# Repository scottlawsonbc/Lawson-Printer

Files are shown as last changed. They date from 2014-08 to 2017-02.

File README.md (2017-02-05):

# Lawson-Printer
Open source high precision 3D printer

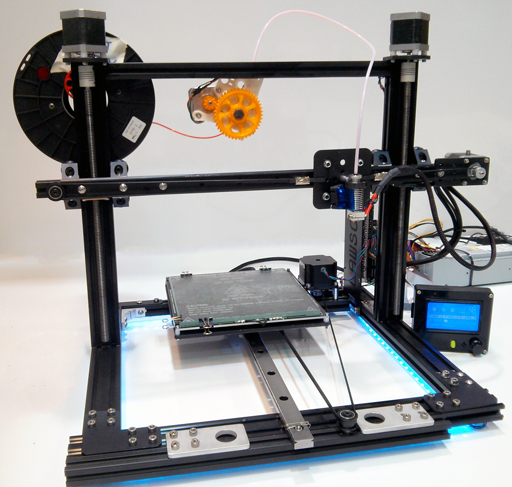
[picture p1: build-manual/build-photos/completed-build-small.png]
completed build


# Introduction
Lawson is a 3D printer design by [Scott Lawson](https://github.com/scottlawsonbc) featuring excellent linear motion accuracy and a mechanically stiff frame. Compared with the MendelMax 2, Lawson eliminates the need for custom sheet metal, slashes build costs, and improves the linear motion of the X, Y, and Z axes. It is easy to source components for the Lawson printer as 95% of the components can be sourced from only two suppliers.

# Overview

## Design Goals
* High accuracy linear motion
* Mechanically stiff frame
* All printable components have purchasable off-the-shelf counterparts
* Easy to source components. 95% of components available from two suppliers to simplify component sourcing

## Cost
The total build cost of the Lawson printer is approximately $900 USD. This is the price for all components needed to build a working Lawson printer including electronics and [[Stepper motor|motors]]. Build costs can be reduced by approximately $120 USD if printed components are used.

## Component Sourcing
See [Lawson Buyer's Guide](http://reprap.org/wiki/Lawson_Buyers_Guide) for component sourcing information.

To simplify component sourcing, 95% of the components can be obtained from only just two suppliers, Misumi and OpenBuilds Parts Store. The parts that cannot be obtained from these suppliers are:
* Hotend + Extruder
* Heated bed + Glass
* Electronics

This gives users the freedom to easily purchase Lawson components themselves, without needing to go through a middle-man supplier selling a kit. 

## X-axis
The x-axis is a belt driven linear stage powered by a NEMA 17 Stepper motor. The axis is constrained by OpenRail which is screwed into a length of 2020 aluminium extrusion. The x-carriage wheels have eccentric spacers that can be adjusted to prevent excessive friction. The belt tension can be adjusted easily by loosening the belt idler and sliding it left or right on the extrusion. While a direct drive extruder can be used, a bowden feed extruder is reccommended because it significantly reduces the mass of the x-carriage, permitting higher acceleration and speed values and reducing resonance.

## Y-axis

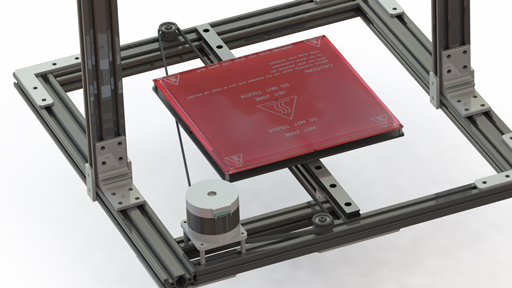
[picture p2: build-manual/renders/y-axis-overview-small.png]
y-axis mechanism


The y-axis is a belt driven linear stage powered by a NEMA 23 Stepper motor and is constrained by a precision Misumi linear slide. Compared to y-axes in other designs such as the MendelMax 2, this triangular belt configuration permits higher speed and acceleration values, reduces component costs, and simplifies construction and maintenance access. The y-axis belt tension can be adjusted by loosening the screws on the NEMA 23 motor and sliding the motor left or right.

The NEMA 23 was selected instead of a NEMA 17 because it permits a simplified mounting configuration and has generally higher performance characteristics.

## Z-axis
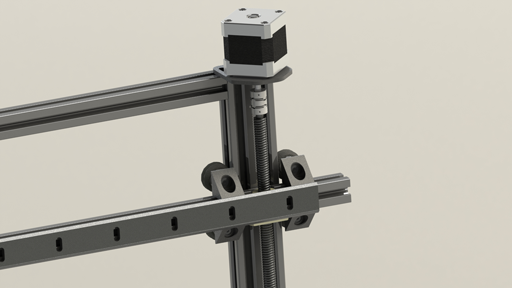
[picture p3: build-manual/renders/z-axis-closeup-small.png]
z-axis closeup


The z-axis is a lead screw driven linear stage powered by two NEMA 17 Stepper motor wired in parallel. The z-axis is accurate to ±150 µm over the full travel. The wheels have eccentric spacers that can be adjusted to prevent excessive friction from overconstaint. 

### Comparison to MendelMax 2
The lead screws in the Lawson printer design have the following accuracy specification:
* ±20µm per revolution (due to [thread drunkeness](http://www.deterco.com/tech_info/conversion/helical.htm))
* ±150µm/300mm accumulated pitch error

In comparison, there is no accuracy specification available for the lead screws that the MendelMax 2 design calls for. As such, the accuracy of the MendelMax 2 lead z-axis cannot be guaranteed.

> Unfortunately our lead screws do not have a tolerance specification for these dimensions. These are medium-grade leadscrews, they are better than the cheap screwes[sic] many people use on 3d printers, but they are not comparable to more expensive high end leadscrews. -Mike [from MakersToolWorks]

## Printable Components
Printable components are highlighted in blue

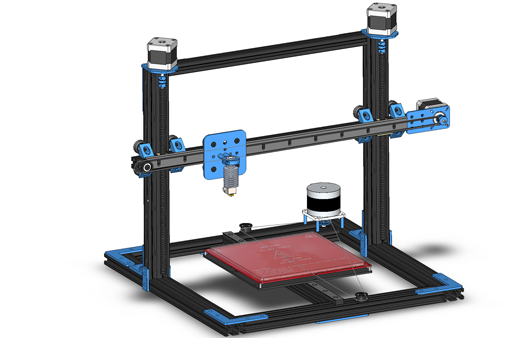
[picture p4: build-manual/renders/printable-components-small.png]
printable components


A number of Lawson components can be 3D printed to reduce build costs, with the caveat that printed components are less stiff than their metal counterparts. Unlike many other RepRap printers, *all printable components are purchasable, but not all purchasable components are printable*. This means that printed components are not mandatory and that individuals without access to 3D printers, or individuals who prefer metal components are able to build a Lawson printer. The use of printed components can save up to approximately $120 USD in build costs.

Printable components:
* **Qty:** 2 **Part:** Heavy duty bracket
* **Qty:** 1 **Part:** GT2 Pulley GPA22GT2060-B-H4
* **Qty:** 1 **Part:** Shaft collar
* **Qty:** 4 **Part:** 2-hole Thin bracket HBLSS5
* **Qty:** 2 **Part:** 4-hole bracket HPTSSL5
* **Qty:** 2 **Part:** 8-hole L bracket HPTLD5
* **Qty:** 4 **Part:** 4-hole L bracket HPTLS5
* **Qty:** 2 **Part:** 4-hole T bracket HPTTS5
* **Qty:** 6 **Part:** 2-hole joining plate
* **Qty:** 1 **Part:** 20mm gantry plate
* **Qty:** 8 **Part:** 90deg vslot corner connector
* **Qty:** 2 **Part:** 5mm x 6mm coupler
* **Qty:** 4 **Part:** Belt crimp clamp

## Electronics
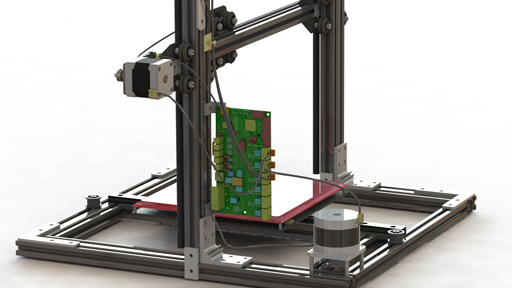
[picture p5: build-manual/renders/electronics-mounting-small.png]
electronics mounting


Almost all RepRap electronics such can be used to control the Lawson. Electronics confirmed to be working include RUMBA, Printrboard, Generation 7 Electronics, Arduino Mega Pololu Shield, and Rambo.

One option for mounting electronics is the rear side of the z-axis aluminium extrusion. The electronics can be conveniently mounted close to the motors and endstops if mounting is on the same side as the x-axis and y-axis motors. With this configuration, there is easy access to the electronics for wiring any maintenance that may be required.

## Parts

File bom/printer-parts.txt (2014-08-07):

REQUIRED PARTS:

	Heavy duty brackets: 		HBLTDW5
	Aluminium extrusion:			HFS5-2060-300
	Linear slide:						SEL2BM20-400
	Spacers:							SMKB4-20

	Belt idler:							http://openbuildspartstore.com/smooth-idler-pulley-kit/
	Belt clamp:						http://openbuildspartstore.com/belt-crimp-clamp/

OPTIONAL PARTS:
	Heat insulating sheets 200x400mm: 				HIFP1-400-200

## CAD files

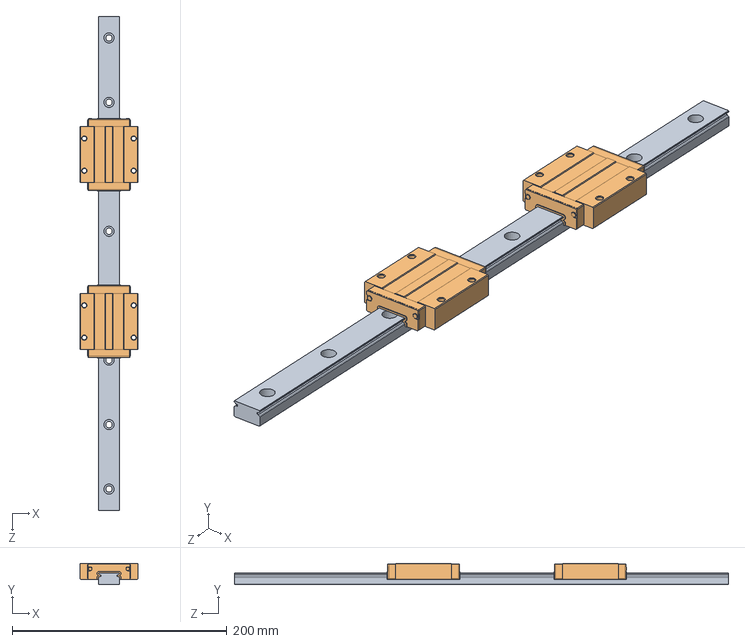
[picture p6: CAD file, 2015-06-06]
solidworks/y-axis-assembly/slide/SEL2BM20-460.sldasm
54.0 x 20.0 x 460.0 mm
SE2BM20-460_r
ELBM20_b x 2

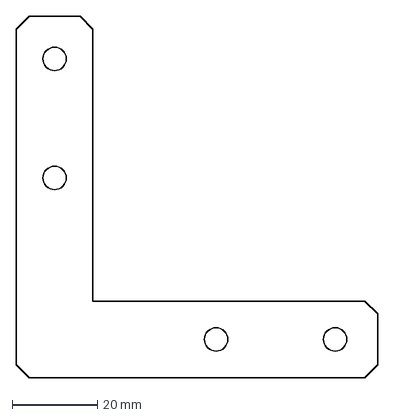
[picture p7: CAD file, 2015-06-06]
dxf-files/4 Hole L Bracket.DXF
85.0 x 85.0 mm

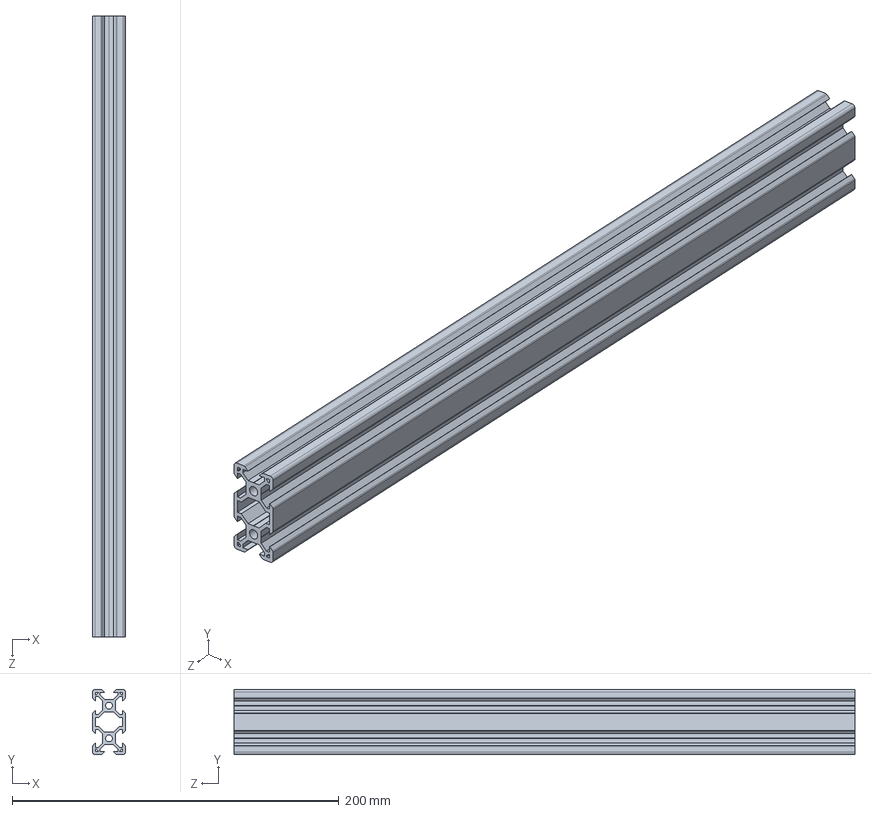
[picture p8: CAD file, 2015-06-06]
solidworks/aluminium-extrusion/openbuilds-extrusion/vslot-2040.SLDPRT
20.0 x 40.0 x 380.0 mm

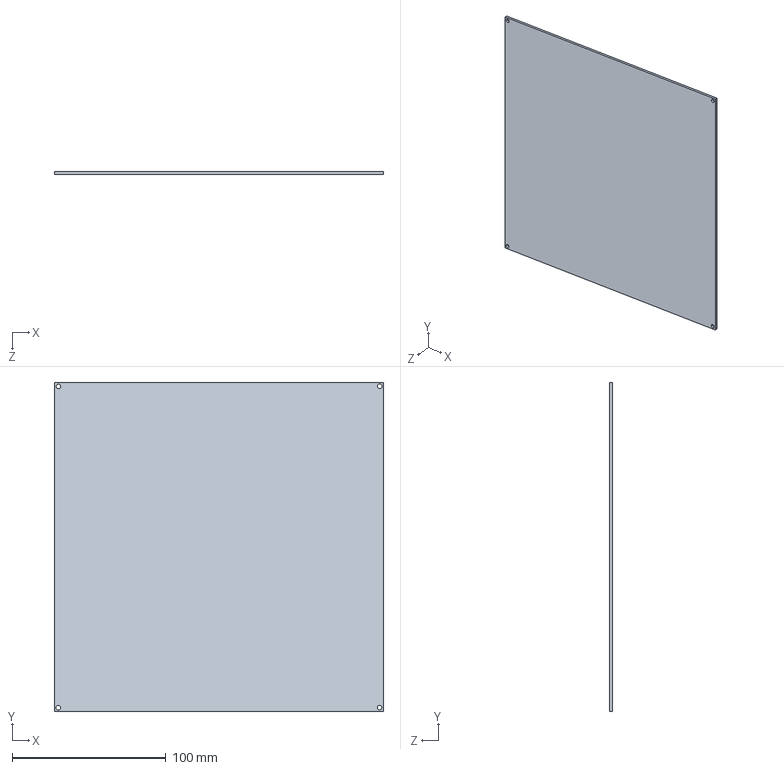
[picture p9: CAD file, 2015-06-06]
solidworks/y-axis-assembly/print-bed/heated-bed.SLDPRT
214.0 x 214.0 x 2.00 mm

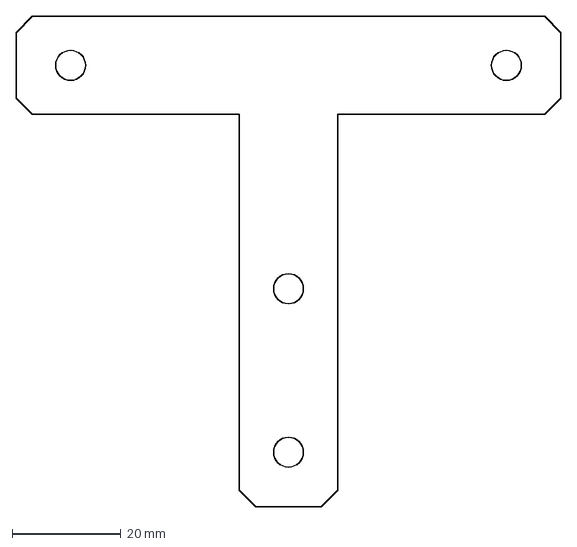
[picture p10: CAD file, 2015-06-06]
dxf-files/4 Hole T Bracket.DXF
100.0 x 90.0 mm

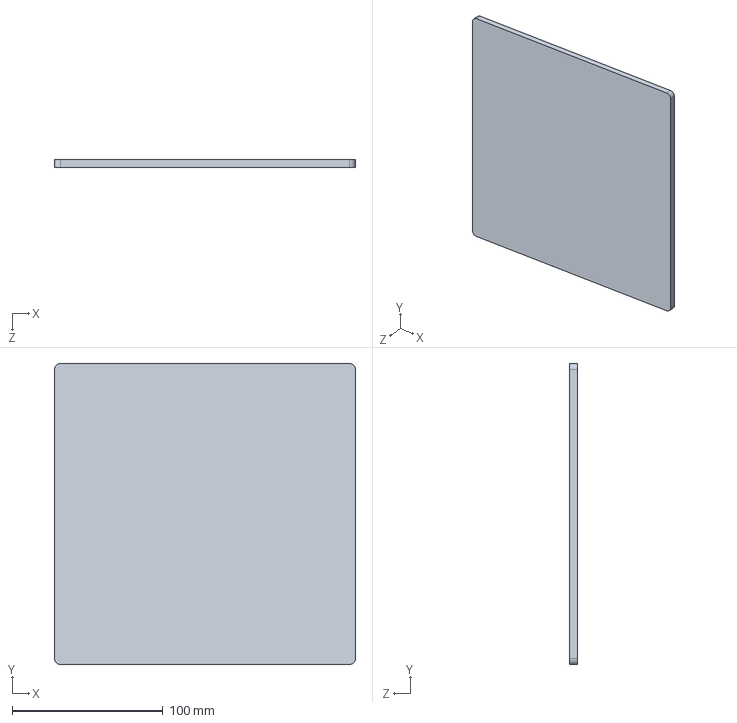
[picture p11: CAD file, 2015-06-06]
solidworks/y-axis-assembly/print-bed/glass-bed.SLDPRT
200.0 x 200.0 x 5.00 mm

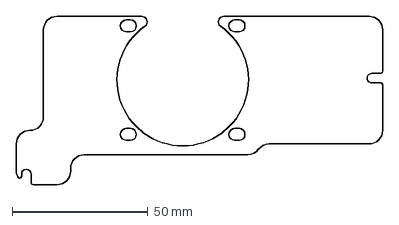
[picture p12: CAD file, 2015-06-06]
dxf-files/electronics-fan-mount.DXF
135.0 x 62.0 mm

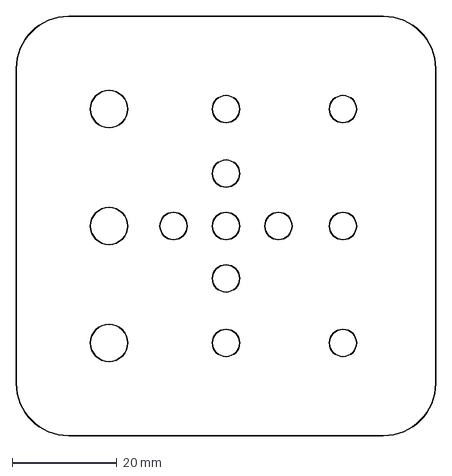
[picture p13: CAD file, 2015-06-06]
dxf-files/OpenRail Universal Gantry Plate - 20mm.DXF
80.0 x 80.0 mm

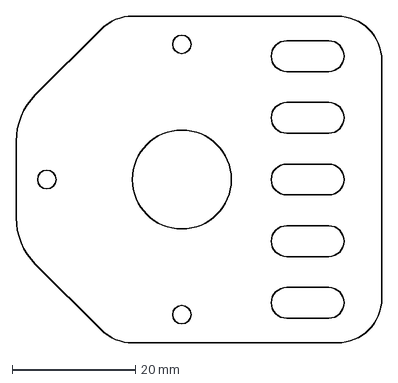
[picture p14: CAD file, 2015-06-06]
dxf-files/motor-mount-bracket.DXF
59.3 x 53.0 mm

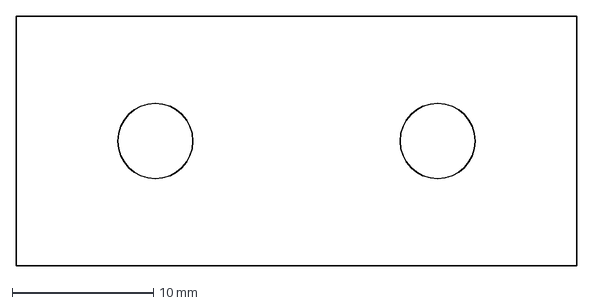
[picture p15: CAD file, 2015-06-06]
dxf-files/2 Hole Joining Strip Plate.DXF
39.7 x 17.7 mm

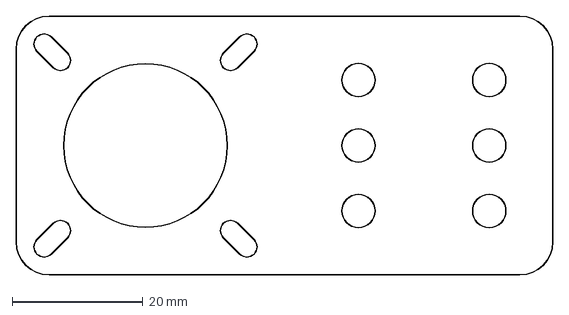
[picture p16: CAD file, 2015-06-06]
dxf-files/V-Slot Motor Mount Plate.DXF
82.0 x 39.5 mm

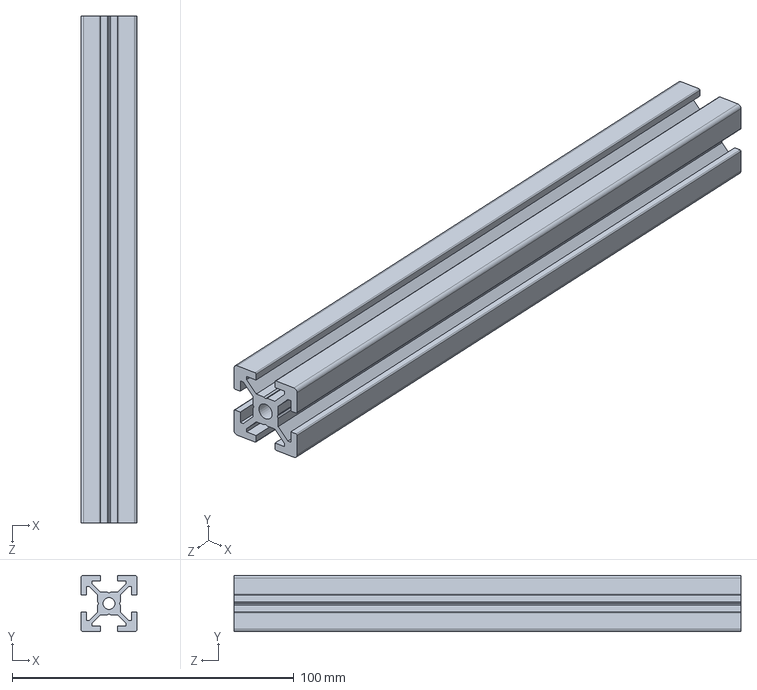
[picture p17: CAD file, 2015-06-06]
solidworks/aluminium-extrusion/misumi-extrusion/2020/2020.sldprt
20.0 x 20.0 x 180.0 mm

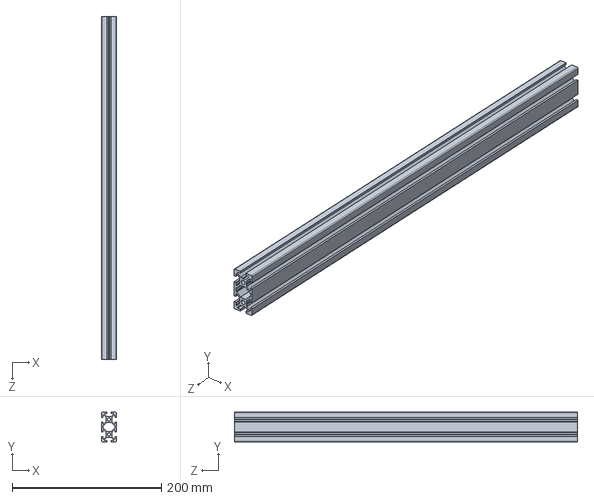
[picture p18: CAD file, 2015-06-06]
solidworks/aluminium-extrusion/misumi-extrusion/2040/HFSB5-2040-460.sldprt
20.0 x 40.0 x 460.0 mm

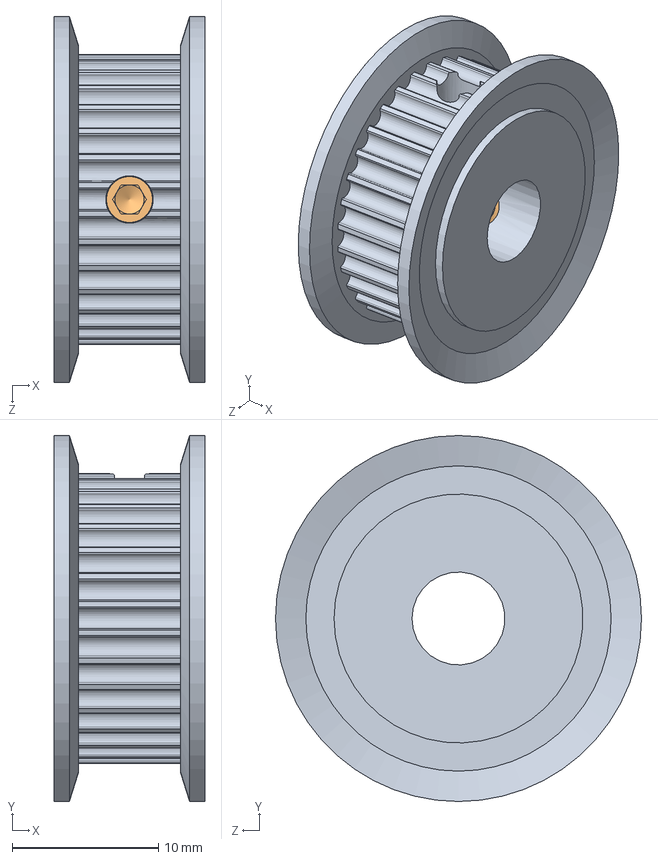
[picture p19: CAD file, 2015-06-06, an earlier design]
solidworks-old/belts-and-pulleys/GT2-for-NEMA-23/GPA32GT2060-A-P6_35.sldasm
10.3 x 25.0 x 25.0 mm
GPA32GT2060-A-P6_35_b
SET-SCREW4-3 x 2

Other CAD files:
solidworks/frame-assembly/frame-assembly.SLDASM
solidworks/y-axis-assembly/slide/SE2BM20-460_r.sldprt
solidworks/y-axis-assembly/slide/ELBM20_b.sldprt
solidworks-old/belts-and-pulleys/idler-assembly/V-slot idler assembly.SLDASM
solidworks-old/bearings/C688ZZ.sldprt
solidworks-old/belts-and-pulleys/GT2-for-NEMA-23/GPA32GT2060-A-P6_35_b.sldprt
solidworks-old/belts-and-pulleys/GT2-for-NEMA-23/SET-SCREW4-3.sldprt
solidworks-old/belts-and-pulleys/GT2-timing-pully-20-tooth.SLDPRT
solidworks-old/belts-and-pulleys/idler-assembly/.25 Inch Aluminum Spacer.SLDPRT
solidworks-old/belts-and-pulleys/idler-assembly/5mm Low Profile Socket Head Screw - Multiple Lengths.SLDPRT
solidworks-old/belts-and-pulleys/idler-assembly/5mm Precision Washer.SLDPRT
solidworks-old/belts-and-pulleys/idler-assembly/5mm x 8mm Low Profile Socket Head Screw.SLDPRT
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

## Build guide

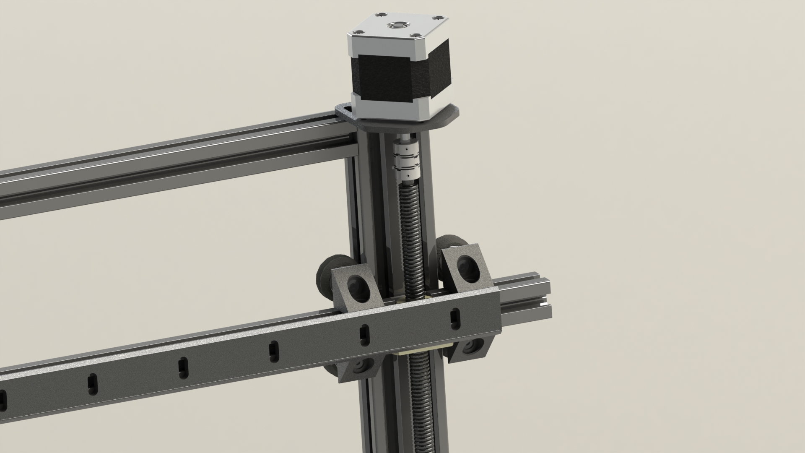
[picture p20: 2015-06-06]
build-manual/renders/z-axis-closeup.JPG

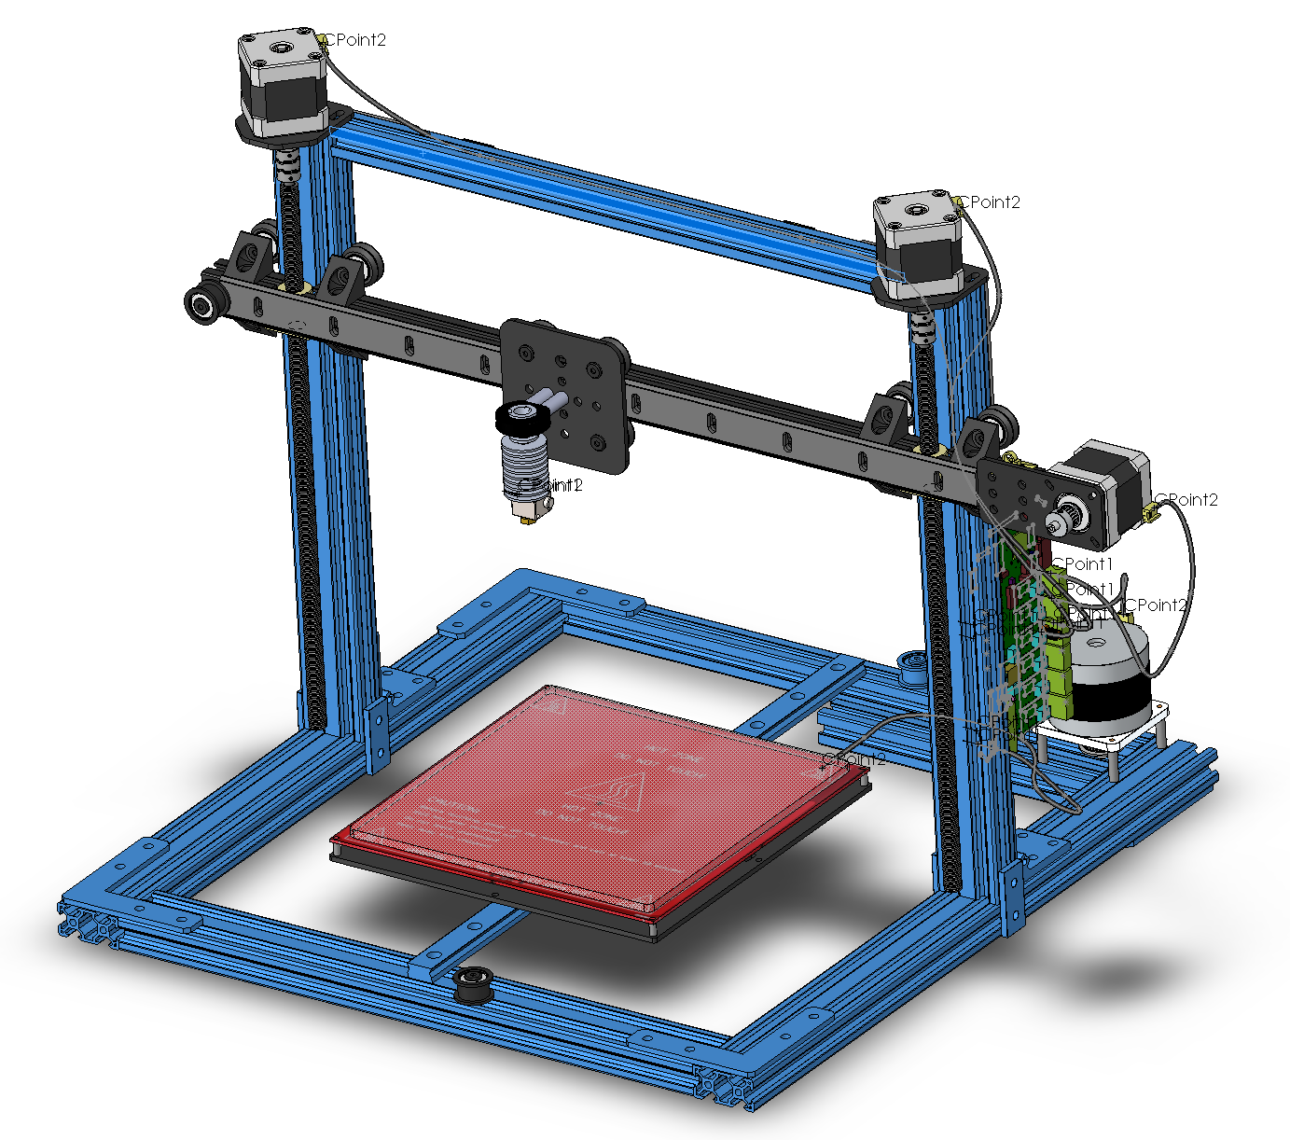
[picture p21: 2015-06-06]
build-manual/renders/base-frame-assembly.png

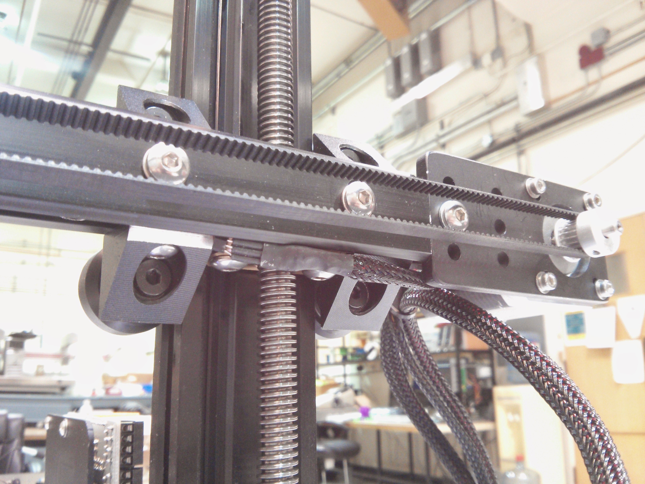
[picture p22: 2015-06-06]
build-manual/build-photos/IMG_20141027_164524.jpg

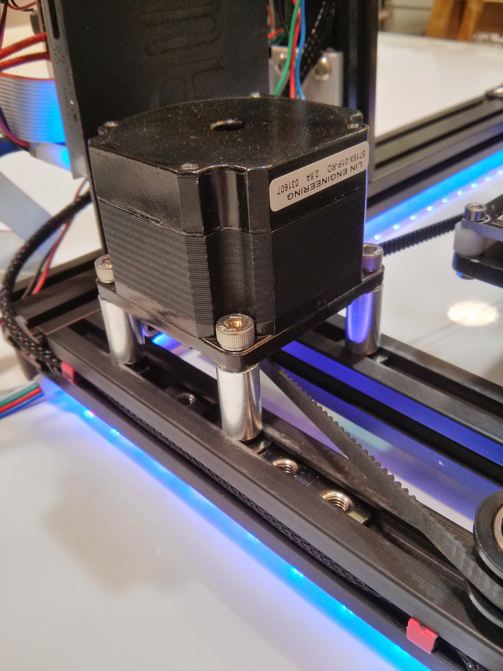
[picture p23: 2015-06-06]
build-manual/build-photos/IMG_20141027_164043.jpg

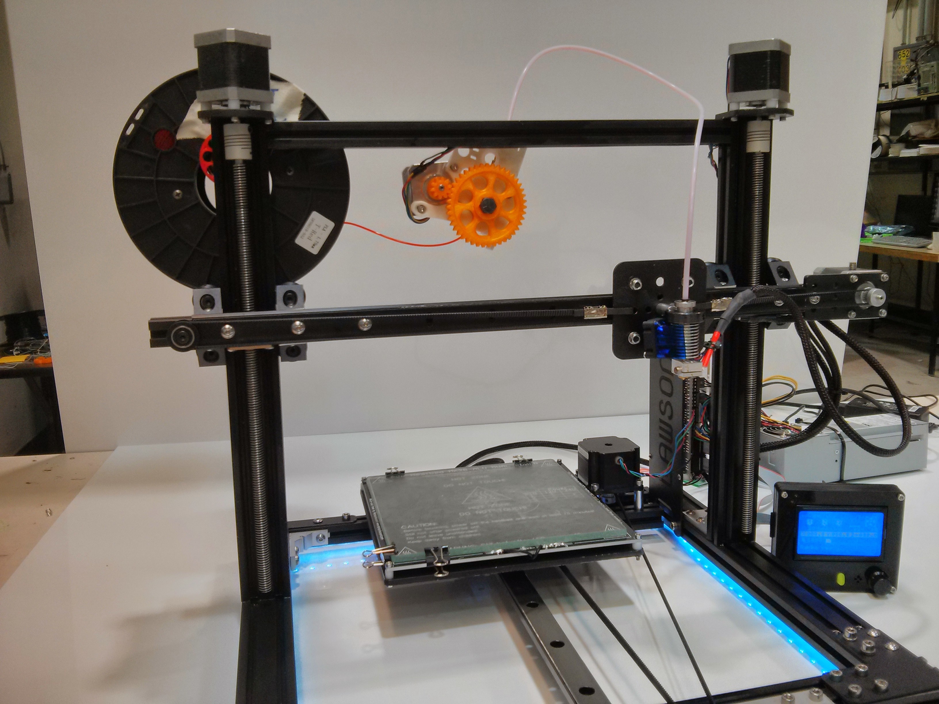
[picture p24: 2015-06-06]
build-manual/build-photos/IMG_20141027_163318.jpg

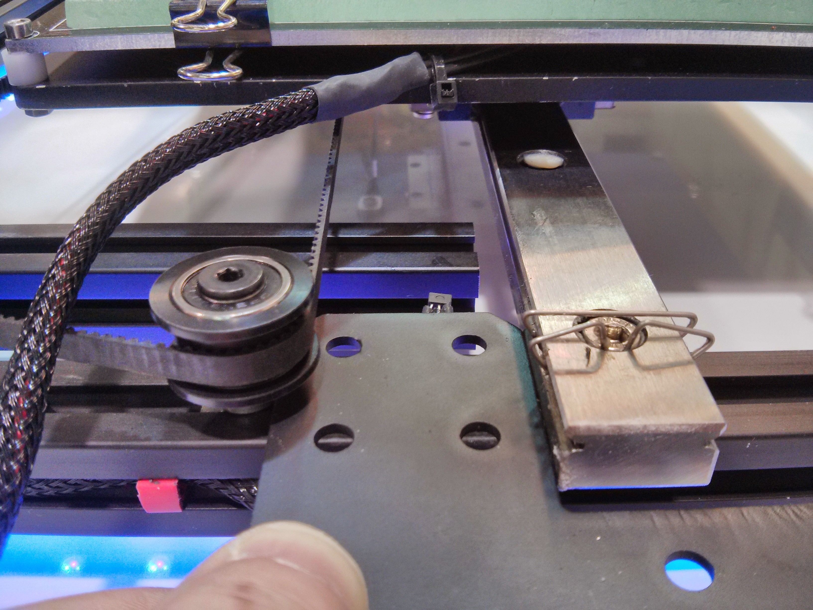
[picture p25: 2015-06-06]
build-manual/build-photos/IMG_20141027_164152.jpg

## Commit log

2017-02-05 Add smaller images of printer build
2017-02-05 Add y-axis photo
